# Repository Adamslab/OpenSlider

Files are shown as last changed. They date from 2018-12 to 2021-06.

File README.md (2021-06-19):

## Openslider XYZ
GithubGIFPt3 GithubGIFPt4

OpenSlider XYZ is a motorized slider with multiple axis of rotation, built using common hardware and 3D printed components.

The goal of OpenSlider is to provide a robust, open source programmable slider platform to fill a variety of needs for hobbyists.

The slider is designed with ease of printing and assembly in mind. No support material is needed. PETG or ABS is recomended.

2040 Roller Carriage Assembly v231_4

Build tutorial: (Work in progress video)
https://www.youtube.com/watch?v=6d8_oJsUrao 

#### Example videos:

[V0.3](https://www.instagram.com/p/CFU9hZHjh4D/) - [V0.3](https://www.instagram.com/p/CBXKDw_DIsY/) - [V0.3](https://www.instagram.com/p/CBQC0gHDRkP/) - [V0.2](https://www.instagram.com/p/Bsbb4AUHvLy/) - [V0.1](https://www.instagram.com/p/BqFpmRJnVI0/) - [V0.1](https://www.instagram.com/p/BqFVQTXnpN9/) - [V0.1](https://www.instagram.com/p/BqJI3UbnU7M/) - [V0.1](https://www.instagram.com/p/Bp2GQGXHDDo/)

#### Interested in supporting the development of OpenSlider?

Join the discord! https://discord.gg/khKH3Cx

Any feedback is greatly appreciated.

[Patreon](https://www.patreon.com/adamslaboratory)

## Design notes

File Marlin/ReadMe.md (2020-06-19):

# Marlinfw.org

OpenSlider runs on Marlin.

A branch of 2.0.x bugfix is included, preconfigured for the SKR 1.3 and TMC2130 drivers.

## GRBL

You can also use GRBL for an alternative control setup if you opt to use an Arduino UNO or Arduino Nano with a CNC shield.

https://github.com/gnea/grbl/releases

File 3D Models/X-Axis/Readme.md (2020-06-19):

# X-Axis

Animation of the slider with X and Y axis assembly (No Z-Axis shown)
2040 Roller Carriage Assembly v231_4

X-Axis Assembly Overview

There might be minor differences between the images and the available .STL files. There is some tolerance in the length of bolts that you can use, so you can usually get away with a slightly longer or shorter bolt than it calls for.

# X-Axis Roller Carriage

3x M5x30mm bolts are used to attach roller wheels to the roller carriage.

On the arm of the roller carriage (The side with only one wheel) there is a slot for an M3x30mm bolt used to tension the X-Axis.

# X-Axis Belt Mount

M3x10mm Bolts are used to fasten the Belt Mount to the Roller Carriage. The bolts feed through holes on the Belt Mount, and into M3 Nut traps on the Roller Carriage.

# X-Axis Feet

The feet use M3 bolts and T-Nuts to attach to the 2040 extrusion.

The LCD attaches using M3 bolts and M3 nuts.

X-Axis Foot Idler
X-Axis Foot Motor

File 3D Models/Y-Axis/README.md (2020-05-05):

There are two mounting systems for the Y-Axis.

One provides support for various mounting plates and a 1/4" bolt. It doesn't support the Z-Axis.



The other is designed to support a third axis. It is still a work in progress.



More to come! Stay tuned, folks.

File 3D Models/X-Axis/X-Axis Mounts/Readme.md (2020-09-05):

## Readme
These components support the X-Axis in one way or another. Alternative feet, tripod mounts, etc.

## Adjustable X-Axis Mount
Github Render 1

Github Render 2

This is a two-piece mount that attaches to the 2040 extrusion on the X-Axis. 
You can use this with a tripod to hold the slider and to position it at an angle.

---
## Other Models

## Tripod mount
It's a quick releast tripod mount, for the X-Axis. If you have a tripod with a quick release arm.

## ENDCAP IDLER (NO FOOT)
Alternate version of the piece that supports the idler bearing, on the X-Axis. This has a lower profile, if you want that for some reason.

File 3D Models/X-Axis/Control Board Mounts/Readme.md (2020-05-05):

Various mounting brackets for control boards.

These connect to the X-Axis Foot (Motor Mount) using 2 of the M3 screw holes that fasten the Nema-17 motor to the frame.

Please suggest control boards on the discord and I will try to support them.

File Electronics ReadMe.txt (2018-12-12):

OpenSlider utilizes an Arduino UNO + GRBL1.1 Shield for motion control.

This is the current control board setup used:
http://osoyoo.com/2017/04/07/arduino-uno-cnc-shield-v3-0-a4988/

I purchased mine through Aliexpress, though it is a widely available setup. You can find this Uno + CNC shield kit on most online retailers, like Amazon, eBay, etc.

There are many other boards available that will accomplish the same thing. The reason I chose the UNO + 4x A4988 setup is because it is extremely affordable, simple to use and it's widely available.

It is possible to also use other stepper drivers instead of the standard A4988. For example, you could upgrade to the TMC2130 for interpolated microstepping and quieter operation. If you are going to use audio from a device mounted directly to the slider, I suggest using TMC2130 drivers to reduce motor noise. I chose A4988 due to the incredibly low cost.

Three NEMA 17 stepper motors and one 28BYJ-48 motor are used. Virtually any NEMA 17 motors will work, as long as they are not extremely low power, or extremely overpowered. I suggest NEMA motors rated to at least 20Ncm.

The software utilized is GRBL, and Universal GCode sender (UGS). GRBL is flashed to the Arduino, and UGS is used to send commands to the Arduino from a connected device.

GRBL: https://github.com/gnea/grbl/releases
UGS: https://github.com/winder/Universal-G-Code-Sender

Bill of Electronic Materials:

3x Nema 17 Stepper Motor
1x 28BYJ-48 (Modified to be a Unipolar motor)
1x Arduino UNO + 4 Axis CNC Shield
4x A4988 Stepper Motor Driver
1x 12V 5A Power Supply

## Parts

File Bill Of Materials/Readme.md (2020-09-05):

# Materials List

Build tutorial: 

https://www.youtube.com/watch?v=6d8_oJsUrao (Work in progress)

## Printing The Frame


The majority of the slider assembly is 3D printed. PETG or ABS is reccomended.

No support material is needed. Calibrating your bridging and horizontal expansion settings will help produce cleaner prints.

0.15mm or 0.2mm Layer Height, 3 to 5 perimeters and 25% infill is reccomended. Use your own judgement.

All of the M3 nut traps are undersized by ~0.1mm, to grab onto the nuts to stop them from falling out during assembly.
You will have to force the M3 nuts into place. This is normal. 
If your printer is poorly calibrated, you might have to use a soldering iron to set the M3 nuts.

The M3 and M5 bolt holes are oversized by at least 0.2mm.
If you're finding that the bolt holes are coming out undersized, you need to calibrate your printer or adjust your horizontal expansion settings. You can also size the holes with a drillbit.

See something you want changed? You can do it yourself using the included .STEP and .F3D files.
There is a .STEP file of the entire slider assembly included in the 3D Models directory.
The slider assembly is free forever with no guarantees or warranty of any kind.

## Nuts/Bolts:

An exact list of required fasteners is coming in the future.
Development of OpenSlider is moving towards four primary fastener types: M3x10mm, M3x20mm, M3x30mm and M5x30mm.

* 5x M5x30mm Bolts
* 3x M3x30mm Bolts
* 1x M3x20mm Bolt
* 5x M5 Nuts
* 5x M3 T-Nuts
* Assorted M3 bolts + hexagonal nuts https://s.click.aliexpress.com/e/_sIpZ55
* 1x GT2 Idler Pulley - (3mm Bore - 20 Teeth)(For X-Axis Idler) - http://s.click.aliexpress.com/e/_d8NUSUX
* 3x GT2 Timing Gear (5mm Bore - Need 1 for each axis of motion) - http://s.click.aliexpress.com/e/_BfZtUX7v

M3 washers (7mm OD) are suggested to help prevent deformation of printed parts but are not required.

## X-Axis Rail:

The X-Axis runs along a V-Slot 2040 aluminum extrusion. You can put two 2020 extrusions together if you do not have a 2040 extrusion.
The longer the extrusion, the more travel distance you will have.

The slider assembly takes approximatly 120mm off of the travel distance.

A 500mm extrusion will give you approximately 380mm of travel.

https://s.click.aliexpress.com/e/_sMJLWJ

## Roller Carriage Wheels

3x V-Slot roller wheels are used for the X-Axis roller carriage.

3x Option B or similar roller wheels are used:

https://s.click.aliexpress.com/e/_rJTbgF

## GT2 Belt

GT2 6mm belt is used.
The length of belt you will need for the X-Axis is double the length of the extrusion that you're using for the X-Axis plus ~50mm.
So for a 500mm X-Axis, you need approximately 1050mm of belt to have enough.

http://s.click.aliexpress.com/e/_d9epYdt

The Y-Axis and Z-Axis uses GT2 belt loops.
The tensioning system will work with 250mm to 264mm belt loops.

https://s.click.aliexpress.com/e/_rQ35Lp

https://s.click.aliexpress.com/e/_sOoTyx

## Bearings & Idler:

Bearings used are 608RS. 8mm ID, 22mm OD

The Y-Axis and Z-Axis use 3 to 4 bearings each (Depending on belt loop length)

Like these: https://s.click.aliexpress.com/e/_s3uaUI

The X-Axis uses a 3mm bore 20 tooth idler pulley: http://s.click.aliexpress.com/e/_d8NUSUX

## Electronics:

For the main branch, an SKR 1.3 is used as the controller with TMC2130 stepper motor drivers.

A 12864 LCD (RepRapDiscount Full Graphic Smart Controller) is used for a display with local controls with SD functionality.

12V 5A power supply to power the slider. 5 Amps is the suggested minimum for 3-axis motion.

(Optional) An ESP8266 module can be added to provide control over WIFI

SKR 1.3 Mainboard with LCD controller and motor drivers: https://s.click.aliexpress.com/e/_sN61d8

SKR 1.3 without LCD: https://s.click.aliexpress.com/e/_sc29Y2

ESP8266: https://s.click.aliexpress.com/e/_dUlDbDn

There are many alternatives for motion control. An SKR board is chosen due to the versatility and price point.

Different stepper motor drivers provide different benefits. 

* A4988 are low cost with reliable performance and 1/16 stepping
* DRV8825 offer high current capability and 1/32 stepping. 
* TMC2130 have sensorless homing, stealthchop and 1/256 stepping. 
* TMC2209 have higher current capability, improved sensorless homing and stealhchop and 1/256 stepping. 

There are lots of other options out there. The choice is up to you, your budget and what features you want.

## Motors

Nema 17 motors are used. One motor is needed for each axis. If you just want X and Y motion, you will only need two motors.

If you expect to do vertical movements with a DSLR, or rapid back and forth movements with high acceleration, 42Ncm or higher is reccomended. For a cellphone, action camera or PiCamera you can use weaker motors.

https://s.click.aliexpress.com/e/_sd4SLV

## Software

The camera slider runs on a branch of Marlin Bugfix 2.0. Marlinfw.org

The version of Marlin included with OpenSlider is configured for the SKR1.3 and TMC2130 drivers. If you are using a different control board or stepper drivers you will have to manually configure Marlin to support your hardware.

It is reccomended to flash Marlin to the SKR using PlatformIO and Visual Studio Code.

https://code.visualstudio.com/

If you decide to use an Arduino UNO/Nano or a similar lower cost setup, you will want to use GRBL1.1 for control instead of Marlin.

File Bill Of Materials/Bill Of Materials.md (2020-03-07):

# Materials List

## Nuts/Bolts:

An exact list of the nuts/bolts required is coming in the future.
* 4x M5x30mm Bolts
* 3x M3x30mm Bolts
* 4x M5 Hex Nuts
* 4x M3 T-Nuts
* M3 bolts + nuts - https://s.click.aliexpress.com/e/_sIpZ55
* 1x GT2 Idler Pulley - 3mm Bore (Toothed)(For X-Axis) - https://s.click.aliexpress.com/e/_dZw7ybJ

## Frame:

The X-Axis runs along a V-Sot 2040 aluminum extrusion. The longer the extrusion, the more travel distance.

The slider assembly takes approximatly 120mm of X-Axis travel. So a 500mm extrusion will give you approximately 380mm of travel.

https://s.click.aliexpress.com/e/_sMJLWJ

The Y and Z axis use printed components and M3 fasteners.

## Roller Carriage Wheels
Wheels will depend on your style of extrusion.

3x Option B or similar roller wheels are used for mine: https://s.click.aliexpress.com/e/_rJTbgF

## GT2 Belt
GT2 6mm belt is used.
The length of belt you will need for the X-Axis is double the length of the extrusion that you're using for the X-Axis.
So for a 500mm extrusion, you need 1050mm of belt to have enough.

The Y-Axis will use a 250mm continuous belt loop. The tensioner will allow for 248-258mm belt loops.

https://s.click.aliexpress.com/e/_rQ35Lp

https://s.click.aliexpress.com/e/_sOoTyx

## Bearings:

Bearings used are 608RS. 8mm inner diameter, 22mm outer diameter, 7mm thick.

Like these:

https://s.click.aliexpress.com/e/_s3uaUI

## Electronics:

An SKR 1.3 is used as the main controller.
TMC2130 drivers are used for the motors.
A 12864 LCD (RepRapDiscount Full Graphic Smart Controller) is used for a display, and local controls with SD functionality.

SKR 1.3 Mainboard with LCD controller and motor drivers:

https://s.click.aliexpress.com/e/_sN61d8

SKR 1.3 without LCD:

https://s.click.aliexpress.com/e/_sc29Y2

The newer SKR 1.4 would also work just fine.  Really any 3D printer control board will work just fine, you will just have to make changes to compensate if you use a different control board.

You can also choose other stepper motor drivers, if you do not want features like sensorless homing or 1/256 microstepping. 

The A4988 are low cost with reliable performance and 1/16 stepping. DRV8825 offer high current capability and 1/32 stepping. TMC2130 have sensorless homing, stealthchop and 1/256 stepping. TMC2209 have high current capability, improved sensorless homing and stealhchop and 1/256 stepping. There are lots of other options out there, too. The choice is up to you and your budget.

## Motors
Nema 17 motors are used. One motor is needed for each axis. 
You do not need exceptionally powerful motors, 28ncm of holding torque is fine.

https://s.click.aliexpress.com/e/_sd4SLV

## Software

The camera slider runs on a branch of Marlin Bugfix 2.0. Marlinfw.org
The version of Marlin included with OpenSlider is configured for the SKR1.3 and TMC2130 drivers.

---------------------------------------------
----
----------------------------------------------
----
----------------------------------------------

# OpenSlider Legacy (Older Versions)
Arduino UNO + GRBL1.1 Shield for motion control.

This is the current control board setup used:
http://osoyoo.com/2017/04/07/arduino-uno-cnc-shield-v3-0-a4988/

I purchased mine through Aliexpress, though it is a widely available setup. You can find this Uno + CNC shield kit on most online retailers, like Amazon, eBay, etc.

There are many other boards available that will accomplish the same thing. The reason I chose the UNO + 4x A4988 setup is because it is extremely affordable, simple to use and it's widely available.

It is possible to also use other stepper drivers instead of the standard A4988. For example, you could upgrade to the TMC2130 for interpolated microstepping and quieter operation. If you are going to use audio from a device mounted directly to the slider, I suggest using TMC2130 drivers to reduce motor noise. I chose A4988 due to the incredibly low cost.

Three NEMA 17 stepper motors are used for motion control. Virtually any NEMA 17 motors will work, as long as they are not extremely low power, or extremely overpowered. I suggest NEMA motors rated to at least 20Ncm.

The software utilized is GRBL, and Universal GCode sender (UGS). GRBL is flashed to the Arduino, and UGS is used to send commands to the Arduino from a connected device.

## Software (Legacy)

GRBL: https://github.com/gnea/grbl/wiki
UGS: https://github.com/winder/Universal-G-Code-Sender

## Belts (Legacy)
The slider uses GT2 timing belts with 2mm pitch. You can use 6mm or 8mm width belts, whichever you prefer. The X-Axis requires one long piece of belt, and the other axis require 250mm continuous belts. You can make continuous belts by attaching the ends of a straight piece of belt cut to the right size, with an adhesive like CA glue.

## Electronics: (Legacy)
3x Nema 17 Stepper Motor
1x Arduino UNO + 4 Axis CNC Shield
4x A4988 Stepper Motor Driver
1x 12V 5A Power Supply

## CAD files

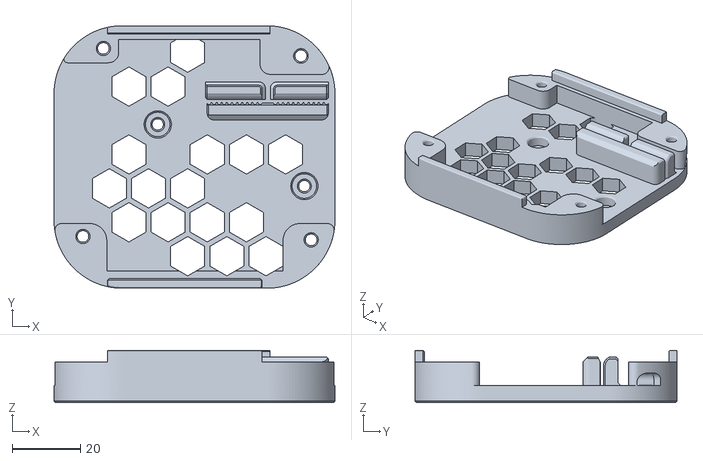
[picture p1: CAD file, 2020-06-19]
3D Models/X-Axis/2. Carriage Belt 2040.stl
82.5 x 77.1 x 15.4

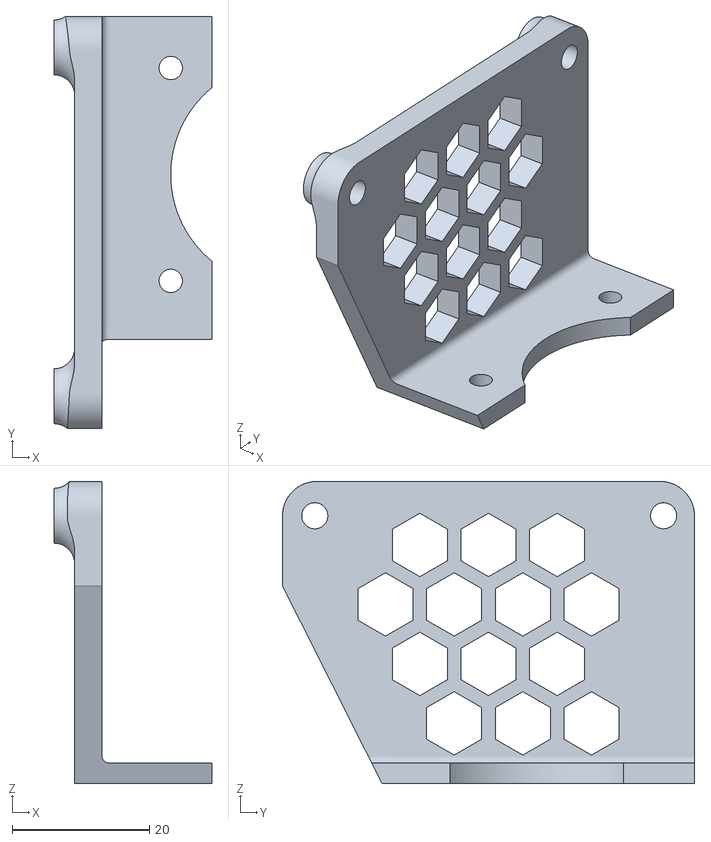
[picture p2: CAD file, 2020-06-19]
3D Models/X-Axis/Control Board Mounts/Ramps 1.4 Mount.stl
23.0 x 60.0 x 44.0

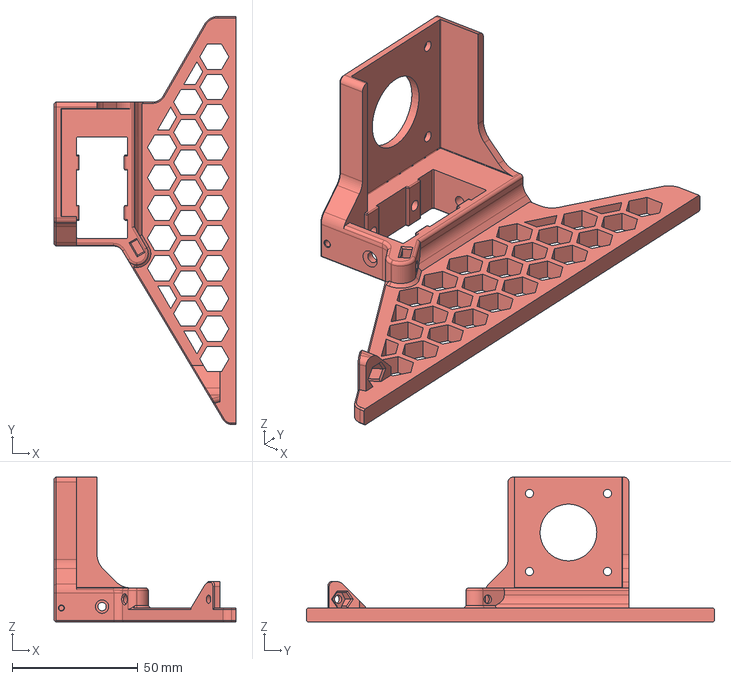
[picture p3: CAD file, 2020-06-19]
3D Models/X-Axis/STEP & F3D/2040 Endcap Motor.step
72.1 x 162.0 x 57.5 mm

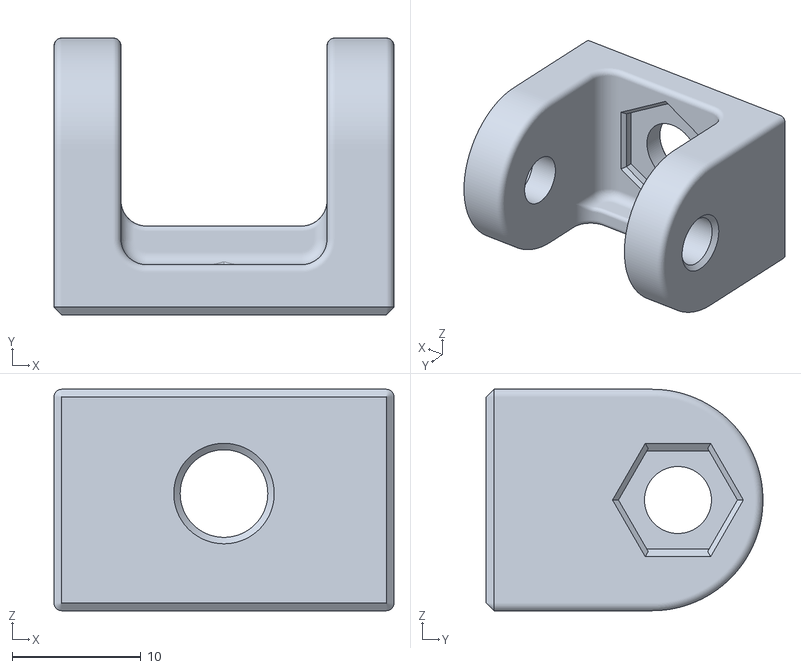
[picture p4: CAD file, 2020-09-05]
3D Models/X-Axis/X-Axis Mounts/Adjustable Mount Pt2.stl
26.4 x 21.5 x 17.2

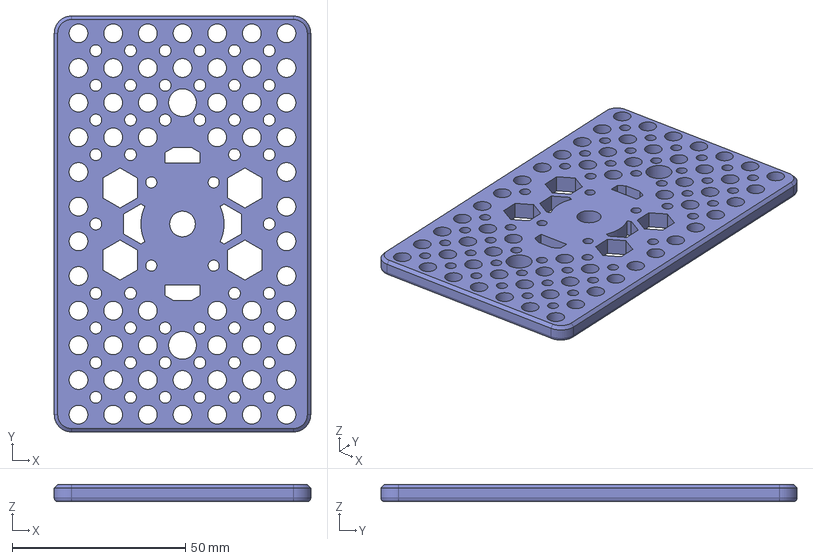
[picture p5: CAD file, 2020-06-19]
3D Models/Y-Axis/STEP & F3D/Mounting Plate Large.step
74.0 x 120.0 x 5.00 mm

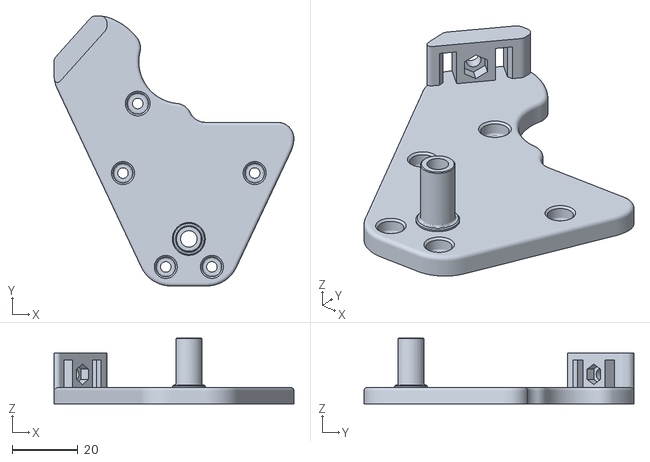
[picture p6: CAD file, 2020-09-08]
3D Models/Y-Axis/Y-Axis Bearing Mount.stl
72.9 x 82.0 x 20.0

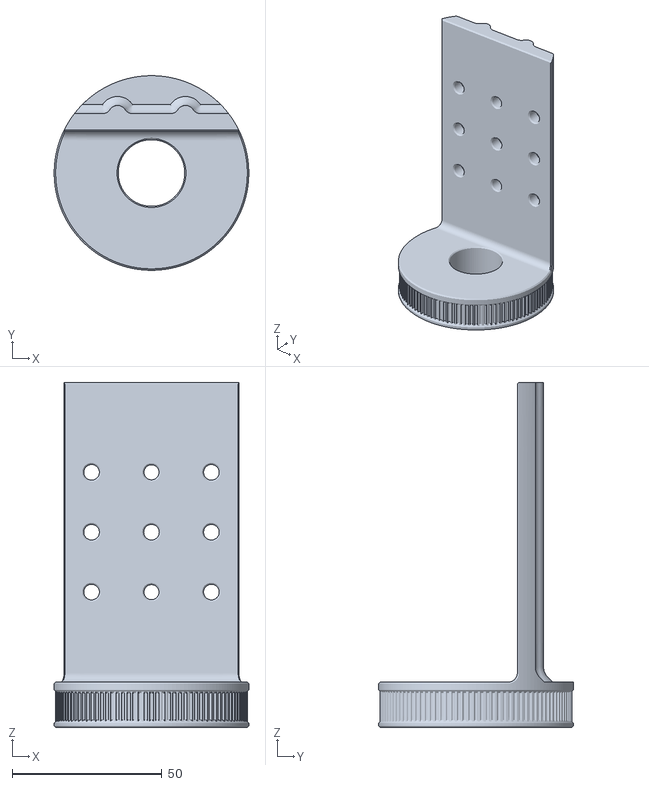
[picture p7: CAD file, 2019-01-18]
3D Models/Z-Axis/Z-Axis Mounting Plate.stl
65.0 x 65.0 x 115.2

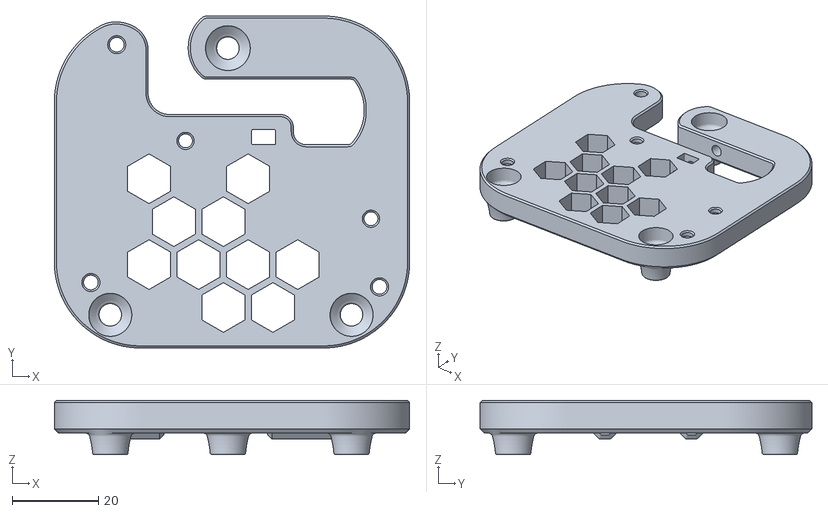
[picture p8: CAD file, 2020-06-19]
3D Models/X-Axis/1. Carriage Roller 2040.stl
82.5 x 77.1 x 12.6

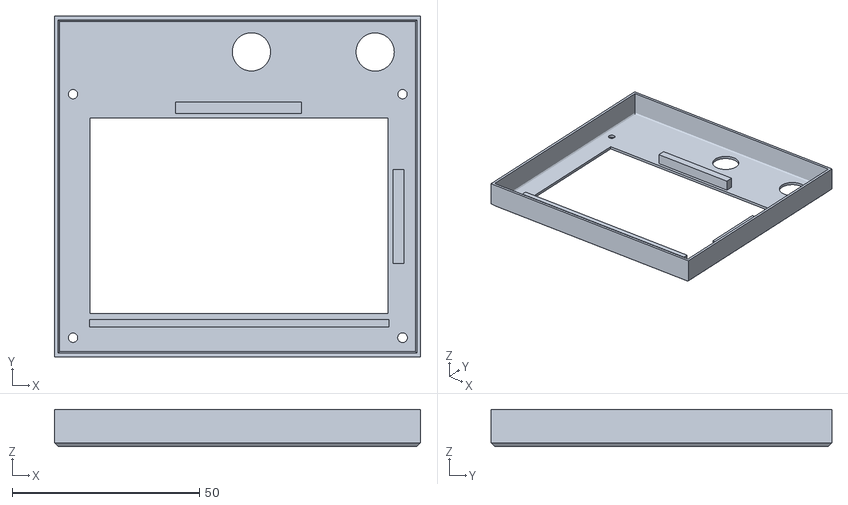
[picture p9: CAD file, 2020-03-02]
3D Models/X-Axis/Control Board Mounts/LCD Frame2.stl
97.7 x 91.0 x 10.0

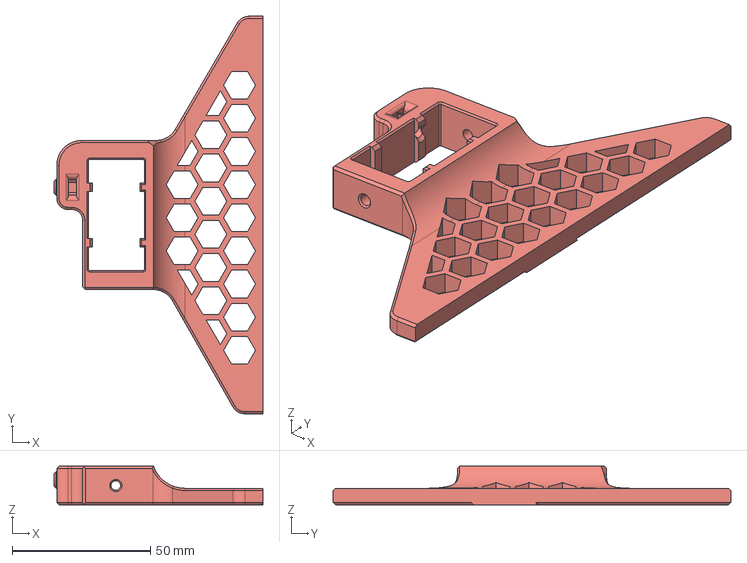
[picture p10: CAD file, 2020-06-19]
3D Models/X-Axis/STEP & F3D/2040 Endcap Idler.step
75.7 x 144.0 x 14.0 mm

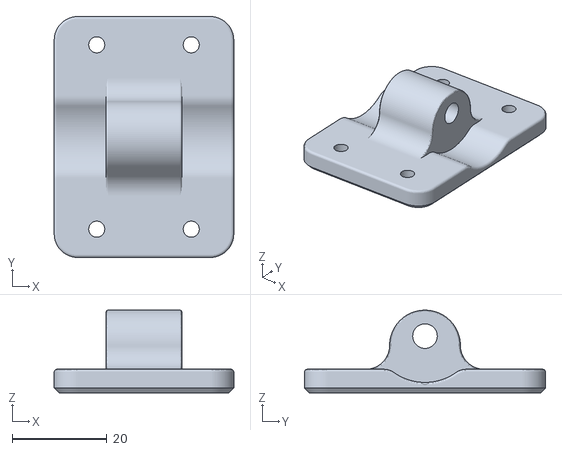
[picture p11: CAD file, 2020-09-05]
3D Models/X-Axis/X-Axis Mounts/Adjustable Mount Pt1.stl
38.0 x 51.0 x 17.5

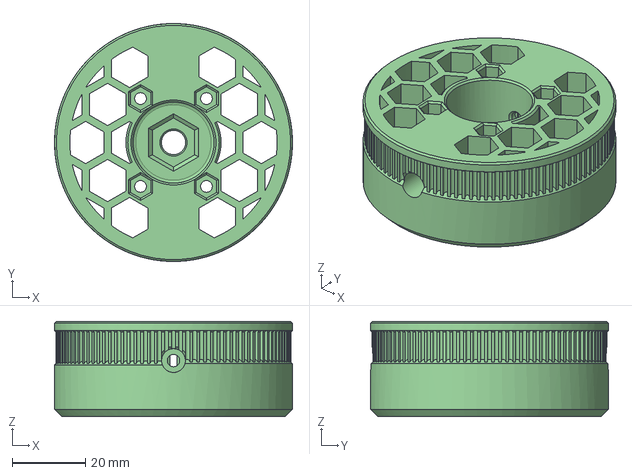
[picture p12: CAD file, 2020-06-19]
3D Models/Y-Axis/STEP & F3D/1. Y-Axis Mount (No Z-Axis).step
65.0 x 65.0 x 26.0 mm

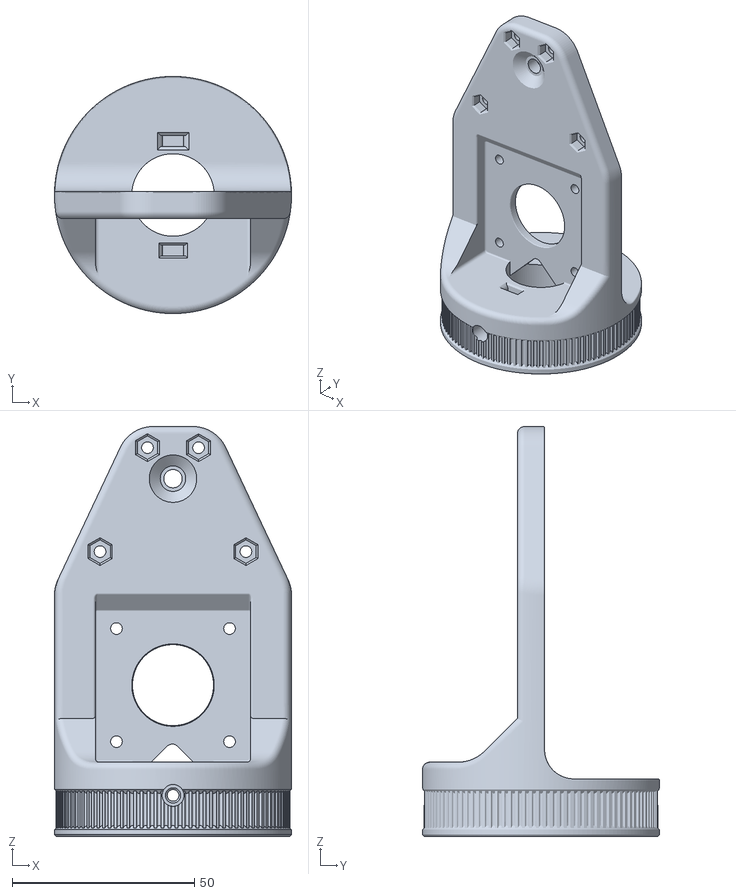
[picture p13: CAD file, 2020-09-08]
3D Models/Y-Axis/Y-Axis Motor Mount.stl
65.0 x 65.0 x 112.4

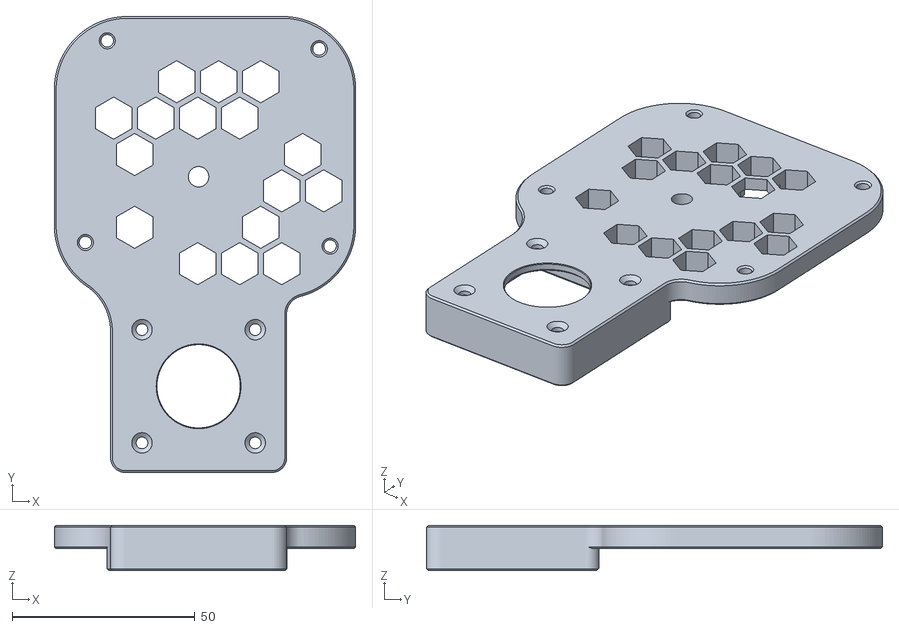
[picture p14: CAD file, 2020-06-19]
3D Models/X-Axis/3. Carriage Motor 2040.stl
82.5 x 124.8 x 12.4

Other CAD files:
3D Models/X-Axis/Control Board Mounts/LCD Frame1.stl
3D Models/X-Axis/STEP & F3D/2. Carriage Belt 2040.step
3D Models/X-Axis/X-Axis Mounts/Endcap Idler 2040 (NO FOOT).stl
3D Models/Y-Axis/STEP & F3D/Mounting Plate Small.step
3D Models/X-Axis/4. Bearing Mount (250-264mm Belt).stl
3D Models/X-Axis/5. Bearing Mount Tensioner.stl
3D Models/X-Axis/6. Endcap Idler 2040.stl
3D Models/X-Axis/7. Endcap Motor 2040.stl
3D Models/X-Axis/Control Board Mounts/Arduino UNO CNC.stl
3D Models/X-Axis/Control Board Mounts/MKS Mini 1.3 Mounting Bracket.stl
3D Models/X-Axis/Control Board Mounts/SKR 1.3.stl
3D Models/X-Axis/STEP & F3D/1. Carriage Roller 2040.f3d
3D Models/X-Axis/STEP & F3D/1. Carriage Roller 2040.step
3D Models/X-Axis/STEP & F3D/2. Carriage Belt 2040.f3d
3D Models/X-Axis/STEP & F3D/2040 Endcap Idler.f3d
3D Models/X-Axis/STEP & F3D/2040 Endcap Motor.f3d
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

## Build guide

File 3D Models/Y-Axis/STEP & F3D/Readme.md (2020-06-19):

.STEP and .F3D files of the Y-Axis assembly

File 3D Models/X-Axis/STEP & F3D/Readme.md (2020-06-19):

.STEP and .F3D files so that it's easier to modify the models for your needs.

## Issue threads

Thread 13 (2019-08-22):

Belt length of pan axis

Merimaa, 2019-08-22:
Hi,

first of all thanks for the design.

I have a problem with the belt length of the pan axis. The 250mm belt is round about 6mm to long. For the tilt axis the 250mm belt fits perfect. Am I doing something wrong?
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

Thanks in advance.

Merimaa

Adamslab, 2020-02-17:
You're right, I made the wrong measurements with my earlier versions. I'm working on releasing a newer version of the X and Y axis that will work for a 248mm to 258mm belt loop length.

Closed 2020-02-17.

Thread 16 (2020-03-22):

Request: Source for models

dushyantahuja, 2020-03-22:
Hi - first of all, thanks a lot for this. I am trying to use equipment that I have lying around, and hence need to modify some of the models. e.g. for the X axis, I would rather use 2020, instead of 2040 - as I have many lying with me. Same for the closed loop belts - I'd like to modify the design to use 200mm belts instead.

Can you please share the editable models.

Adamslab, 2020-04-11:
Hi,

Sorry for the delay in responding to this issue. I'll upload the files in a few other formats so they can be edited. What format do you need?

dushyantahuja, 2020-04-11:
No problems - I edited the STLs using TinkerCAD :-)
However, step files / fusion3D files would be nice.
------------------
Dushyant Ahuja

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

Adamslab, 2020-05-05:
Glad to hear you got it working. If you'd like to add your modified version to the Github project that would be great. I added .STEP files for the X-Axis to the github.

dushyantahuja, 2020-05-05:
Thanks.
Modified models are in my fork:
https://github.com/dushyantahuja/OpenSlider

Can't submit a pull request - as I've deleted off all the Marlin stuff, and don't know enough about github to be able to submit a partial pull request.

Adamslab, 2020-05-06:
I can add your files and provide credit back to you.

dushyantahuja, 2020-05-06:
Be my guest.

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

Closed 2020-05-05.

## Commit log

2018-11-14 Basic readme for X-Axis components.
2018-11-14 Adding X-Axis .STL files
    Uploading some .STLs. Included are:
    X-Axis 2020 Roller Carriage - This is the roller carriage that slides along a 2020 extrusion. Two of these are needed for the X-Axis.
    X-Axis 2020 Carriage Body - This is the primary body that the roller carriages attach to. The GT2 belt for the X-Axis attaches to this component.
    X-Axis 2020 Mounting Plate - This is the top plate that attaches to the carriage body. It provides a number of holes compatible with M3 nuts/bolts for mounting things.
    200mm 2020 Rail.stl - This is an example 2020 rail used for modeling/reference purposes. It is 200mm long.
    400mm 2020 Rail.stl - This is an example 2020 rail used for modeling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
    [200mm 2020 Rail.stl, 400mm 2020 Rail.stl, X-Axis 2020 Carriage Body 001.stl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]
2018-11-14 Basic Y-Axis Readme.
    Establishing a basic readme.
2018-11-14 Adding Y-Axis Motor Mounting Plate
    Testing a new version of the Y-Axis motor mounting plate.
    [Y-Axis Motor Face Plate Bearing Mount 001.stl]
2018-11-14 Updating Readme.
    Updated the readme, with a disclaimer regarding printing the current X-Axis components.
2018-11-14 Update X-Axis Readme.txt
2018-11-18 Updated
    Updated X-Axis models to current revision.
    [X-Axis 2020 Carriage Body 002.stl, X-Axis 2020 Mounting Plate 002.stl, X-Axis 2020 Roller Carriage 002.stl]
2018-11-18 Updating
    Updating Y-Axis models to current versions.
    [Y-Axis Bearing Mounting Bolt 001.stl, Y-Axis Motor Body Cover 001.stl, Y-Axis Motor Face Plate Bearing Mount 002.stl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]
2018-11-18 Create Z-Axis Readme
2018-12-10 Fixing 2020 rail model and adding 2040
    [200mm 2020 Rail.stl, 200mm 2040 Rail.stl, 400mm 2020 Rail.stl]
2018-12-12 Uploading current 2020 X-Axis Models
    [X-Axis 2020 Carriage Body 002.stl, X-Axis 2020 Mounting Plate 002.stl, X-Axis 2020 Roller Carriage 002.stl]
2018-12-12 Rename X-Axis Readme.txt to Readme.txt
2018-12-12 Rename Y-Axis Readme.txt to README.md
2018-12-12 Rename Z-Axis Readme to README.md
2018-12-13 Updated roller carriage design
    Added a combined roller carriage.
    [2040 Roller Carriage - Double.stl, 2040 Roller Carriage - Single.stl]
2018-12-13 Removing obsolete design
    [2040 Roller Carriage.stl]
2018-12-13 Updated readme reflecting new carriage design
2018-12-13 Updated Carriage Belt Mount Design
    [2040 Roller Carriage Belt Mount.stl]
2018-12-13 Adding new X-Axis Motor Mount Design
    [2040 Motor Mounting Plate.stl]
2018-12-13 Adding Bearing Mount + Screw
    [2040 Bearing Mount Screw.stl, 2040 Motor Mounting Plate Bearing Mount.stl]
2018-12-13 Deleting old single roller carriage design.
    [2040 Roller Carriage - Single.stl]
2018-12-13 New 2040 Roller Carriage design
    [2040 Roller Carriage - Double.stl]
2018-12-13 Removing obsolete mounting plate - use motor mount
    [2040 Roller Carriage Top Mounting Plate.stl]
2018-12-13 Created basic BOM.
2018-12-13 Updated roller carriage
    [2040 Roller Carriage - Double.stl]
2018-12-13 Cleaning up ReadMe, moving BOM
2018-12-17 Uploading Latest Carriage Design
    [2040 Roller Carriage - Double.stl]
2018-12-17 Updating X-Axis To Current Version
    [2040 Bearing Mount Screw.stl, 2040 Motor Mounting Plate Bearing Mount.stl, 2040 Motor Mounting Plate.stl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]
2019-01-18 Delete 2040 Bearing Mount Screw.stl
    This part is no longer needed for the 2040 X-Axis. It is replaced by a metal M5 bolt.
    [2040 Bearing Mount Screw.stl]
2019-01-18 Delete 2040 Roller Carriage - Double.stl
    Replacing with new version, under a slightly different name.
    [2040 Roller Carriage - Double.stl]
2019-01-18 Delete 2040 Endcap X-Axis Motor Mount.stl
    Getting rid of old version.
    [2040 Endcap X-Axis Motor Mount.stl]
2019-01-18 Delete 2040 Idler Pulley End Mount.stl
    Obsolete version
    [2040 Idler Pulley End Mount.stl]
2019-01-18 Updating X-Axis Files to V0.2
    [X-Axis Bearing Mount Tensioner.stl, X-Axis Bearing Mount.stl, X-Axis Belt Mount.stl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]
2019-01-18 Updating X-Axis readme for V0.2
2019-02-28 Adding X-Axis motor mount/endcaps
    [2040 Endcap - Idler Mount.stl, 2040 Endcap - Motor Mount.stl]
2019-06-08 Added F3D and STEP files
    [Reference - OpenSlider Assembly V2 v12.f3d]
2020-02-17 Moving BoM
2020-02-17 Update Bill Of Materials.md
2020-03-02 Update and rename Readme.md to Bill Of Materials.md
2020-05-05 Rename Bill Of Materials.md to Readme.md
2020-05-06 Add files via upload
    Small fix
    [4. Bearing Mount (250-264mm Belt)).stl]
2020-05-06 Add files via upload
    Okay it's really fixed this time
    [4. Bearing Mount (250-264mm Belt).stl]
2020-05-20 Removing Legacy Files
    Removing legacy files.
    Small adjustment to BoM - Changing M3x15mm to M3x20mm.
    [2040 Bearing Mount Screw.stl, 2040 Endcap - Idler Mount.stl, 2040 Endcap - Motor Mount.stl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]
2020-05-24 Updating X-Axis Motor Foot
    [7. Endcap Motor 2040.stl]
2020-05-25 Adding updated idler foot
    [6. Endcap Idler 2040.stl]
2020-05-25 Updated Files
    [1. Carriage Roller 2040.stl, 2. Carriage Belt 2040.stl, 3. Carriage Motor 2040.stl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]
2020-05-25 Adjusted idler position by 1mm
    [6. Endcap Idler 2040.stl]
2020-06-18 Add files via upload
    Adding .STEP file for assembly
2020-06-19 .STEP of complete assembly
2020-08-19 Add adjustable tripod mount
    [Adjustable Mount Pt1.stl, Adjustable Mount Pt2.stl]
2020-09-07 Delete 4. Bearing Mount (250-264mm Belt).f3d
    Not importing properly - need to fix
    [4. Bearing Mount (250-264mm Belt).f3d]
2020-09-08 Add files via upload
    Fixing files
    [Tensioner.stl, Y-Axis Bearing Mount.stl, Y-Axis Motor Mount.stl]
